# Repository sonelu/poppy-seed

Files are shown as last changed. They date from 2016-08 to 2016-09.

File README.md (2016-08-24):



# Poppy-Seed

This is the little sibling (sister?) of the [Poppy Humanoid](https://github.com/poppy-project/poppy-humanoid) robot developed by the [Poppy Project](https://github.com/poppy-project) team.

At this moment it is in alpha stages and the only thing that can be promissed is that it doesn't catch fire in the first 2 hours of (very limited) operation. Those that are interested to participate in the development of this robot are wellcome, but I cannot stress ehough that things are not in a final form and most of the work involved is not trivial in nature. In time we expect certain items to be provided ready-made instead of needing to hack them from scratch, therefore simplifying the construction.

## Preliminary documentation
Before going into the details of the project there are a few documents that may be useful to read:
* [Torque and design]: a document that explains the main assumption behind the belief that Poppy Seed will work.
* [High level design]: the main design considerations for Poppy Seed.
* [3D Printing guide]: as one of the goals of Poopy Seed is to be printed on a home 3D printed, I included in this document the main tips about printers, materials, finishing and others.

## Poppy Seed
Here are the main links to the project:
* [BOM](hardware/BOM.md). The list of parts needed for the building of a Poppy Seed robot
* [3D Model](https://cad.onshape.com/documents/56e0876fe4b0cd61903da4dc/w/bd94978c48e4f7f7abc728f0/e/cfad6e13d76618b39ab2a28a). This is the link to the OnShape 3D model of the Poppy Seed robot. You can access it freely and in case you want to participate in the development, please send me a share request.
* [3D Parts](hardware/3d parts/). This is the main page for the STLs for the robot.
* [Assembly guide](docs/assembly/README.md). This is the entry page for the robot assembly guide.
* [Electronics](hardware/electronics/). This is the entry page for the electronics used in the project. Please read carefully before starting this project.
* [Setup]. A document providing the steps needed to setup the robot for use.

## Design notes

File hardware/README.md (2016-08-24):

# Hardware

This section contains information about the hardware parts that are needed for the build of your Poppy Seed.

First have a look at the [BOM](BOM.md) file and make sure you understand all the parts that are needed. As this is a very early version of the robot some parts are custom-built. Some things are easy, but there are also parts that require soldering  and tools that you might not have laying around. So please take your time and read through the documents and understand what are the expectations <u>before</u> you place the orders for the materials needed.

If you plan to print the 3D parts youself read the document [3D Printing Guide] and make sure you understand the complexities of this process. If this is your first time in 3D printing I don't think it is a good idea to have Poppy Seed as your first project. A good knowledge of your 3D printer capabilities and limitations will save a lot of effort, time and money. The directory <b>"3D parts"</b> contain all the STLs that are needed. 

Once you have the parts you can start putting the robot together. The [Assembly guide](../docs/assembly) will walk you through this process, including the setup of the electronics.

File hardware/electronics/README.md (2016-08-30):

# Electronics

This section provides details about the custom or customised electronics used in Poppy Seed.

* [Hot-Swap board](hotswap.md): this boards are placed in the shins and they are used to control the power flow from the batteries to the Dynamixel bus allowing us to hot-swap the batteries
* [XL hub](xlhub.md): this is a small board that allows us to connect up to 5 XL cables together and has standard 4mm mounting holes that will give us the ability to position it on the side of a servo
* [Custom HAT with Dynamxiel bus controller, power regultors and 9DOF IMU]: this HAT (board that fits on top a Raspberry Pi) is a temporary solution until Hipi becomes avaialable
* [Audio amplifier]:
* [Raspberry Pi on a diet]: this is a standard Raspberry Pi with the USB and Ethernet connectors removed and replaced with some simple JST 4-pin connectors. This reduces significatly the weight of the board and saves a lot of space for connectivitiy (since the USB connectors are extremely bulky for our need)
* [A custom USB adapter for dongles]
* [A custom USB cable - very short for the Dynamixel bus controller]

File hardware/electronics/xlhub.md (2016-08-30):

# Dynamixel XL hub

Unlike the AX bus, there is no original [Robotis hub](http://www.robotis-shop-en.com/?act=shop_en.goods_view&GS=1398&GC=GD080300) that allows you to connect together several Dynanixel cables for XL bus. It is quite easy to put this together with a little bit of soldering skills.

You will need:
* a small prototyping board - preferrably one with stripes
* 5 [MOLEX microblade board connectors](http://uk.farnell.com/molex/53253-0370/header-2-0mm-3way/dp/1756921)

As tools you will need:
* a soldering iron
* solder
* small pliars
* a drill with a 4mm bit
* a hand saw (to trim the board)

The board as seen on the component face looks like this:

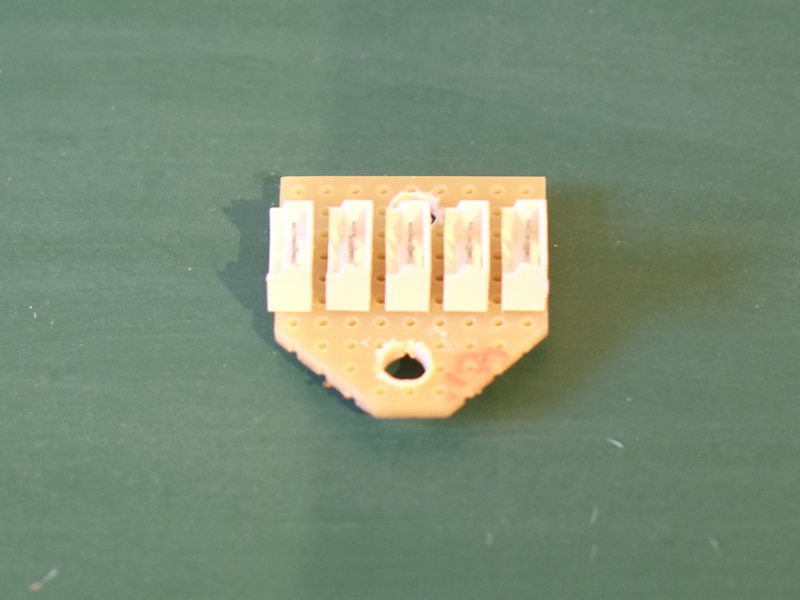
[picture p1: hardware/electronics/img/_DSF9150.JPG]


Cut the board so that you have 9 x 10 holes availalable. We will solder the 5 MOLEX connectors alon those 9 holes while the vertical 10 holes will allow us to drill 2 4mm holes at aproximately 18mm distance.

Solder the 5 MOLEX connectors on the boards and connect them pin to pin. The following picture should give you an idea of the back of the board:

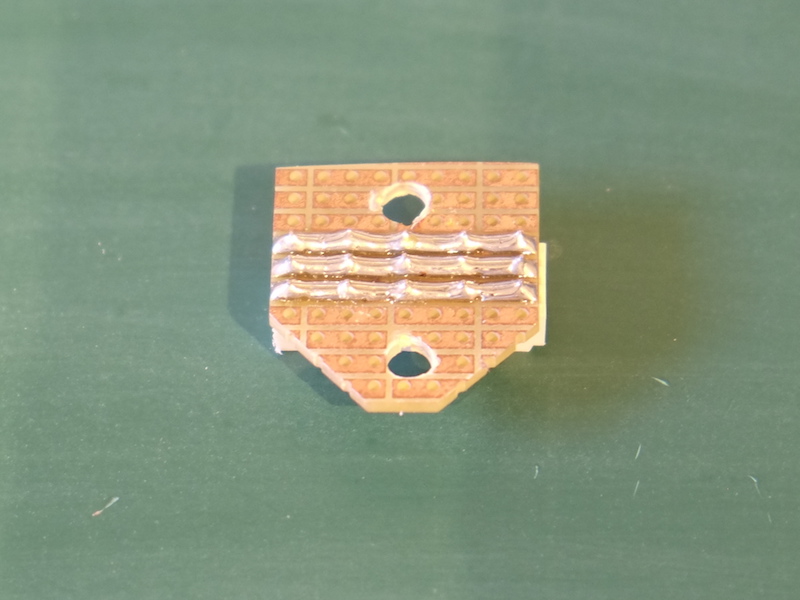
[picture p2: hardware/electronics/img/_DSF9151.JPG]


The board has normally 2.54 pitch and the MOLEX connectors have 2mm. Don't be put off by this: gently push the exterior connector a little so that they can be placed in the holes, then presss firmly the connector onto the board. You will see that you can press it all the way until the bottom of the connector is in contact with the board. Solder the connector on the back. Then, looking at the pins of the connector you will see that they have been bent towards the center of the connector. Take a small pliers and simply straighten them back to the vertical position. Repeat this for all the 5 connectors.

Now make two 4mm holes at 7 holes distance = 17.78mm. This is good enough to allow us to mount this board on the side of a servo using the mounting holes that have 18mm. When making this holes the best is to use 2mm, 3mmm and then 4mm drills instead of going straight to the 4mm drill. You will have less changes for your drill to slip one side or the other.

When you're done cut the corners of the board as you see in the pictures. This will reduce the risk of faulting moving parts from the robot while the board is in position close to joints.

You will have to prepare two of these boards for a Poppy Seed, one for the upper torso and one for the lower torso.

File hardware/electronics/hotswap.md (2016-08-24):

# Hot-Swap board

For Poppy Seed we will use LiPo batteries to power the Dynamixel bus as well as the electronics. We will use two LiPo batteries (2S - 1000mA) each one located in the foot. Using two batteries provides a number of advantages:

* equal distribution of weight
* more capacity (2 x 1000mA)
* ability to swap the batteries one by one thus reducing the need to power down the electornics (mainly the Raspberry Pi)
* because the batteries a positioned in the lowest possible place it reduces the position of the center of mass for the robot, improving stability

In order to be able to use 2 LiPo batteries in parallel and expecially to allow hot-swapping of the batteries (ex. removing one of the batteries that is discharged and replacing it with a fresh battery) we need to control the way the current flows between these batteries. If we connect the batteries blindly in parallel, when batteries are discharged (ex. aprox. 7V or bellow) and one of the batteries is replaced with a new battery (ex. aprox. 8.4V) the difference in potential between the two batteries will produce a so called "rush current" - practically it is as if the new battery is shorted. This is extrmely dangerous as the currents can reach (for short period of time, true) 2-3 times more than the dicharge current that the battery can support.

To avoid this scenario we need to place in series with the battery a diode that allows the current to flow in only one direction (from the battery to the consumer) thus blocking the flow towards the battery (which happens for instance in the case of the discharged battery). A simple diode might foot the bill here provided that it is dimensioned corectly for the power disipassion needed. A typical silicon diode has a forward voltage of 0.7V - meaning we will loose 0.7 V from the battery voltage. In our case this is not very good news because we will loose aprox 10% of the 2S LiPo voltage which is not acceptable. Additionally with an expected current of 2A going through this diode we would have a power dissipation of 0.7V x 2A = 1.4W which will be quite a hefty diode. And a hot one indeed.

The alternative is to use a diode with a forward voltage as lower as possible. This is what the Schottky diodes are for: their forward voltage is in the range 0.35V, some even lower. That means lower power consumption (and heat) as well as less loss of potential from the battery.

The most elegant solution though is to use the Texas Instruments' [SM74611KTTR](http://uk.farnell.com/texas-instruments/sm74611kttr/hot-swap-controller-30v-to-263/dp/2492333) hot swap controller that is designed for the current flow in photovoltaic pannels. This is an actually complex device that includes a high power MOSFET (that ensures a low forward voltage) and a sophisticated charge pump and controller that ensures a very low power consumption and very high efficiency. The forward voltage these "smart bypass diodes" is typically 28mV!

The board for the Poppy Seed hot-swap is build with such a smart diode and it includes in addtion:

* 2 [MOLEX connectors 52253 Micro-Latch](http://uk.farnell.com/molex/53253-0370/header-2-0mm-3way/dp/1756921)
* One 2 pin standard 2.54 pin header
* a small prototyping board

The two Molex connectors and the smart diode is placed on one face of the board:

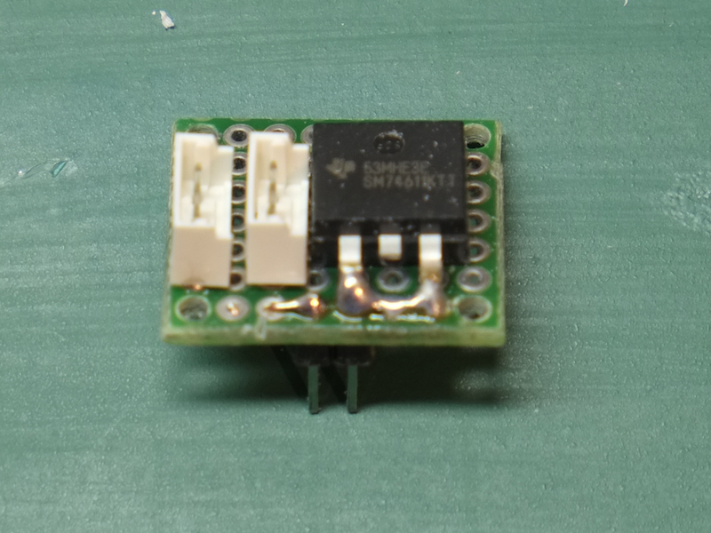
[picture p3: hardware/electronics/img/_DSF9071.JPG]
_DSF9071


While the 2-pin head is on the other side:

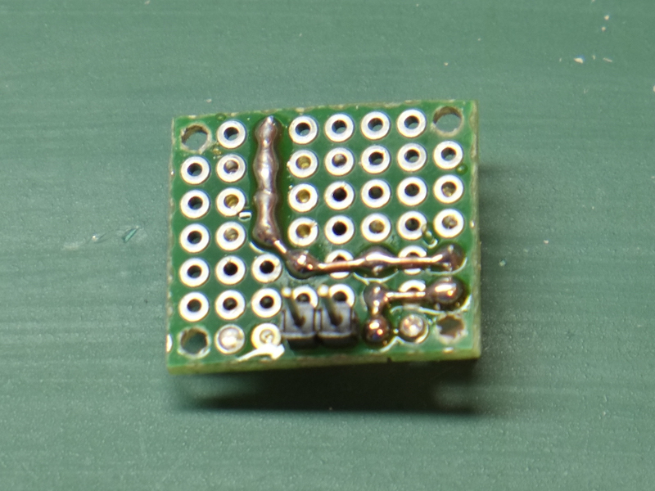
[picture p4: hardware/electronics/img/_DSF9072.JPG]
_DSF9072


The connections are pretty intuitive:

* the pin-head as seen from the side with the parts (the first picture above) is connected with the right pin to the + of the battery and the left pin to the - of the battery. This is controlled by the hole at the back of the shin that allows you to connect the battery in only one way
* the + from the pin is connected to the anode of the diode (the pins)
* the cathode of the diode (the DAP area) then connects to the VCC pins of the Dynamixel bus (center of the two MOLEX connectors)
* the - from the battery connects to the GND pins of the Dynamixel bus (the lower pins in the first picture)
* the 2 MOLEX pins are connected pin-to-pin as you can see in the second picture

The board has 4 holes in the corners with 17.78mm horizontal distance between them (7 standard 0.1' holes) and 15.24mm vertical distance (6 holes). This is the distance between the supports in the shin.

When the battery is connected in the 2 pins on the back side it will inject the voltage into the Dynamixel bus that is connected to the MOLEX connectors. If there is already voltage in the bus (for example there is already another battery on the chain) and that voltage is higher than the voltage of our battery then the diode will break the circuit and our battery will no longer be connected to the bus (this is the case of a discharged battery). If the voltage of our battery is higher than the existing voltage of the chain (if any) than the diode will let the current flow through the circuit, powering the bus.

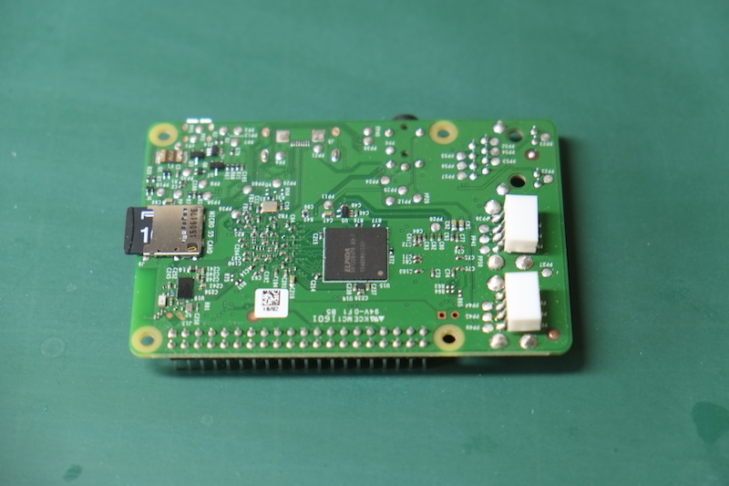
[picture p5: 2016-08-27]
hardware/electronics/img/_DSF9110.JPG

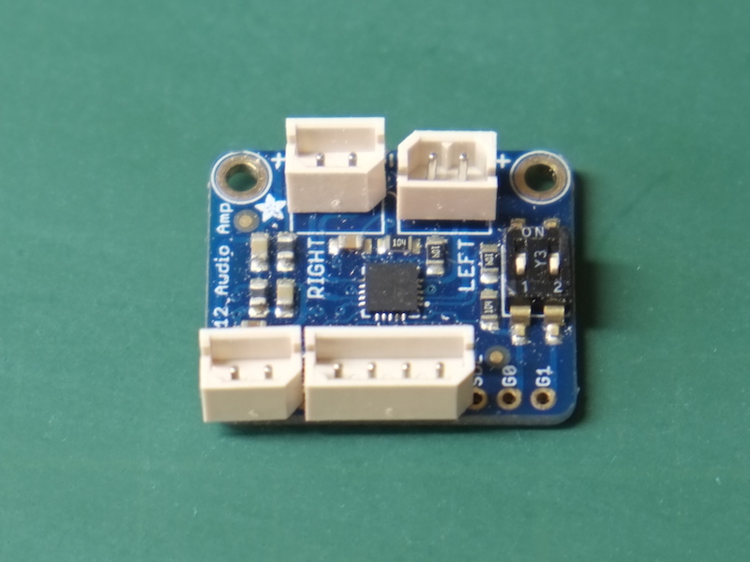
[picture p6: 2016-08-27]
hardware/electronics/img/_DSF9108.JPG

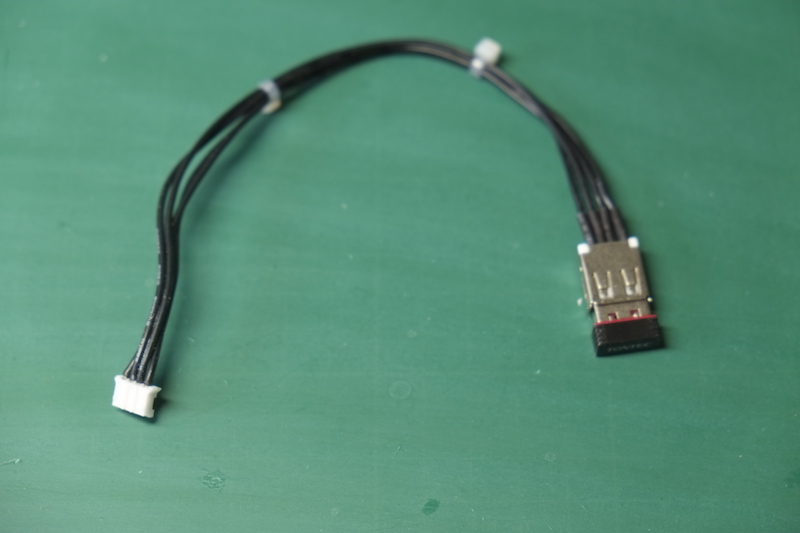
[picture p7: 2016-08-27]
hardware/electronics/img/_DSF9114.JPG

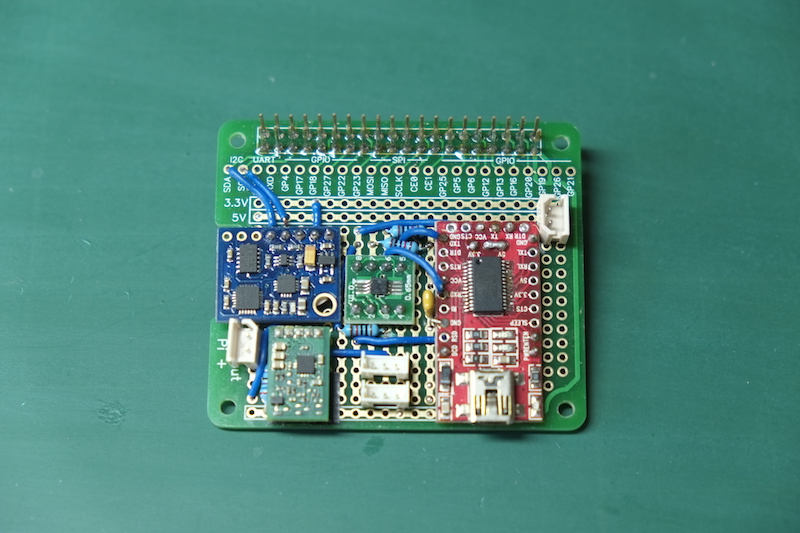
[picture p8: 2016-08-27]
hardware/electronics/img/_DSF9112.JPG

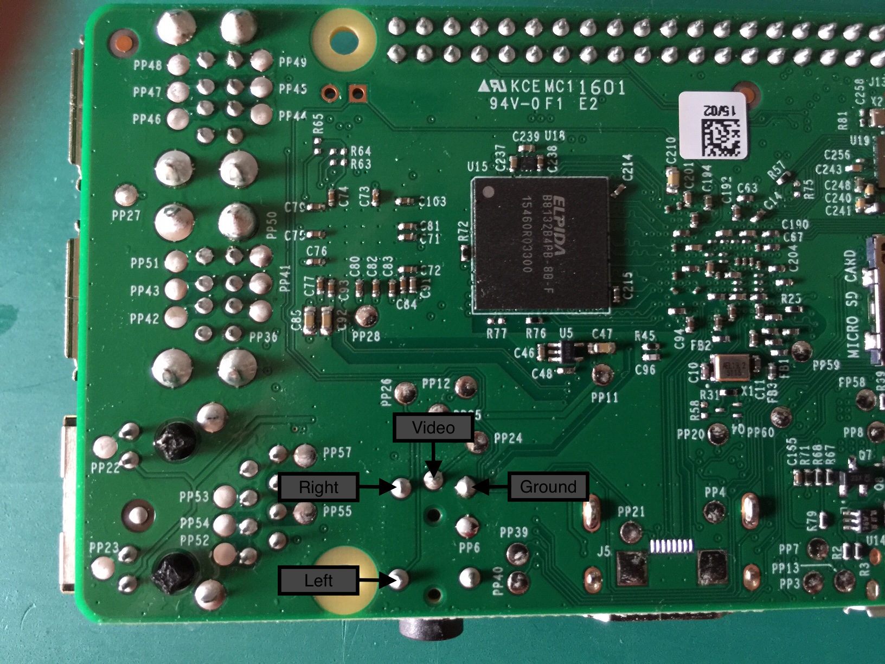
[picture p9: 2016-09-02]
hardware/electronics/img/audio.jpg

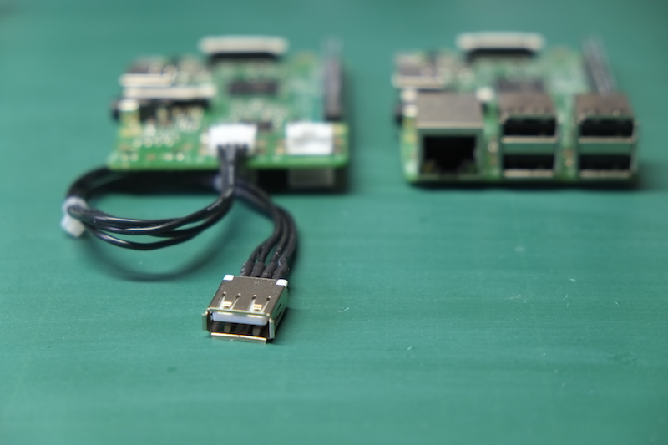
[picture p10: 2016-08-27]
hardware/electronics/img/_DSF9115.JPG

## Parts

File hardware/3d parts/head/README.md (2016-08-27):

# 3D Parts for Head

These are the STL files for the parts that are needed to build the Poppy's head.

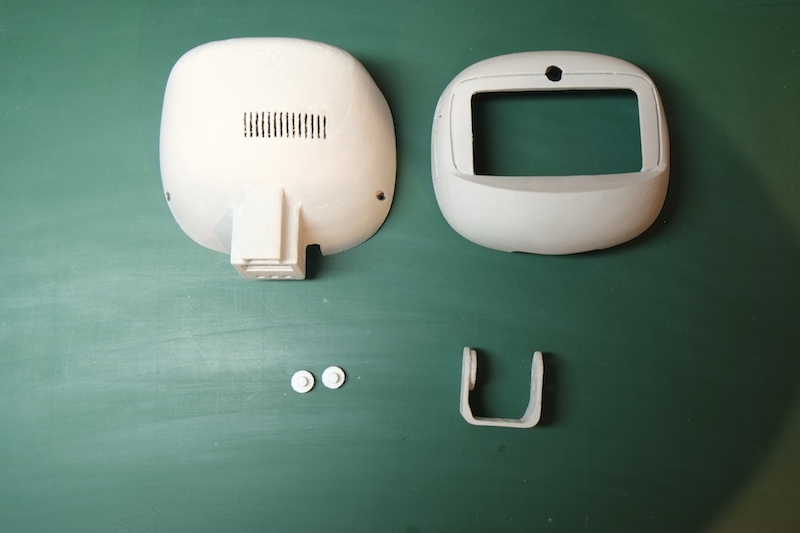
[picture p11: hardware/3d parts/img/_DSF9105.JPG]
Head


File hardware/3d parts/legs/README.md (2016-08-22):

# 3D Parts for Legs

These are the STL files for the parts that are needed to build the Poppy's legs.

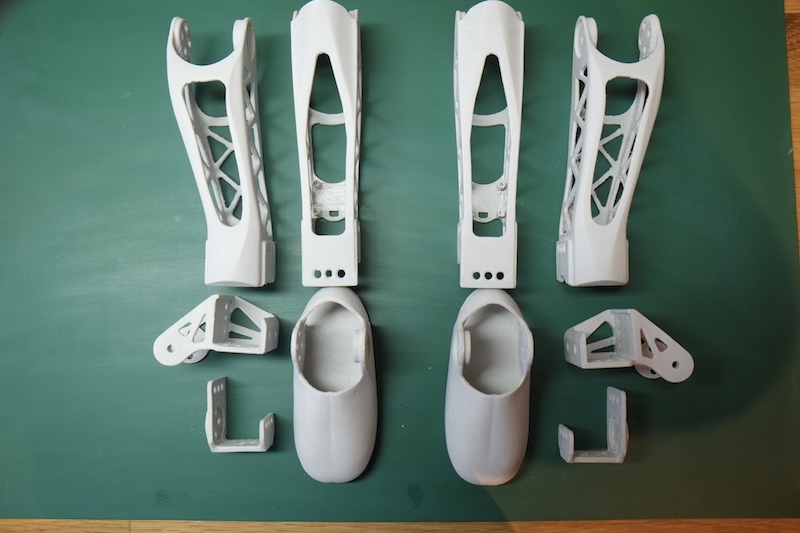
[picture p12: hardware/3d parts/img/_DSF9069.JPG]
Legs


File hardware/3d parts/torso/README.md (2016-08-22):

# 3D Parts for Torso

These are the STL files for the parts that are needed to build the Poppy's torso.

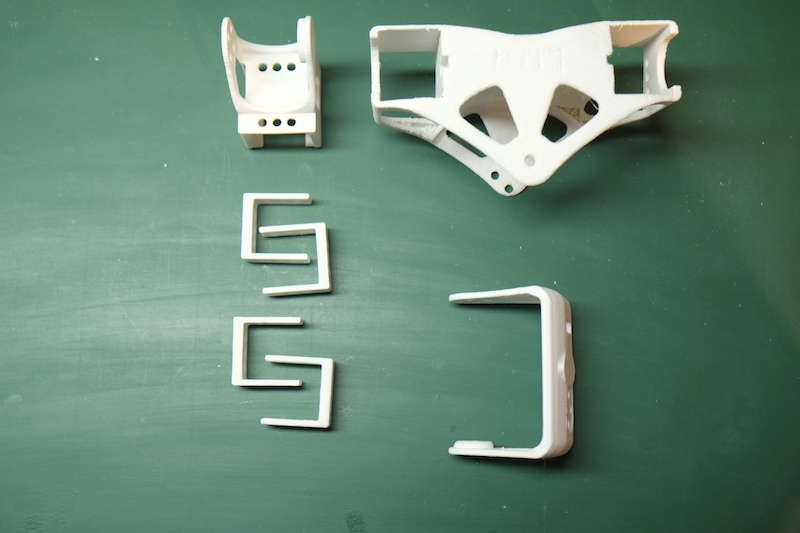
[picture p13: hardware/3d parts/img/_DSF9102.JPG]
Torso


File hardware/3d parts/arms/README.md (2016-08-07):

# 3D Parts for Arms

These are the STL files for the parts that are needed to build the Poppy's arms.

Arms

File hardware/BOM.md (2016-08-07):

# Poppy Seed Bill of Materials

This is the list of materials that are needed for the Poppy Seed:
<table>
<tr>
<th width=25%>Part</th align=center><th>Quantity</th><th>Description</th>
</tr>
<tr><td colspan=4><b>Servomotors</b></td></tr>
<tr><td><a href="http://support.robotis.com/en/product/actuator/dynamixel_x/xl_series/xl-320.htm">Dynamixel XL-320</a></td><td align=center>25</td><td>All the motors for Poppy Seed are XL-320, a very cost effective variant of Dynamixel servomotors that have impressive capabilities in a diminutive body. The servos are widely avaialble at all retailers that specialise in robotics as well as Amazon and eBay. Please refer to the document [Torque and design] to understand more about why they might work in this project.</td></tr>
<tr><td colspan=4><b>3D printed parts</b></td></tr>
<tr><td><i>Arms</i></td></tr>
<tr><td>Hand left</td><td align=center>1</td><td><a href="https://github.com/sonelu/Poppy-Seed/blob/master/hardware/3d%20parts/arms/hand%20left%20small.stl">link to the STL</a></td></tr>
<tr><td>Hand right</td><td align=center>1</td><td><a href="https://github.com/sonelu/Poppy-Seed/blob/master/hardware/3d%20parts/arms/hand%20right%20small.stl">link to the STL</a></td></tr>
<tr><td>Forearm left</td><td align=center>1</td><td><a href="https://github.com/sonelu/Poppy-Seed/blob/master/hardware/3d%20parts/arms/forearm%20left%20small.stl">link to the STL</a></td></tr>
<tr><td>Forearm right</td><td align=center>1</td><td><a href="https://github.com/sonelu/Poppy-Seed/blob/master/hardware/3d%20parts/arms/forearm%20right%20small%20(check).stl">link to the STL</a></td></tr>
<tr><td>Upper arm</td><td align=center>2</td><td><a href="https://github.com/sonelu/Poppy-Seed/blob/master/hardware/3d%20parts/arms/upper%20arm%20small.stl">link to the STL</a></td></tr>
<tr><td>Arm connector</td><td align=center>2</td><td><a href="https://github.com/sonelu/Poppy-Seed/blob/master/hardware/3d%20parts/arms/arm%20connector%20small.stl">link to the STL</a></td></tr>
<tr><td>Shoulder left</td><td align=center>1</td><td><a href="https://github.com/sonelu/Poppy-Seed/blob/master/hardware/3d%20parts/arms/shoulder%20left%20small.stl">link to the STL</a></td></tr>
<tr><td>Shoulder right</td><td align=center>1</td><td><a href="https://github.com/sonelu/Poppy-Seed/blob/master/hardware/3d%20parts/arms/shoulder%20right%20small.stl">link to the STL</a></td></tr>
<tr><td><i>Body</i></td></tr>
<tr><td>Chest</td><td align=center>1</td><td>[link to the STL]</td></tr>
<tr><td>Spine</td><td align=center>1</td><td>[link to the STL]</td></tr>
<tr><td>Abdomen</td><td align=center>1</td><td>[link to the STL]</td></tr>
<tr><td>Dual XL mount</td><td align=center>4</td><td>[link to the STL]. Used to connect two XL servo is a 90 degrees angle.</td></tr>
<tr><td>XL idle</td><td align=center>2</td><td>[link to the STL]. Used to provide the idle support for a dual XL-320 combination.</td></tr>
<tr><td><i>Legs</i></td></tr>
<tr><td>Foot left</td><td align=center>1</td><td>[link to the STL]</td></tr>
<tr><td>Foot right</td><td align=center>1</td><td>[link to the STL]</td></tr>
<tr><td>Shin left</td><td align=center>1</td><td>[link to the STL]</td></tr>
<tr><td>Shin right</td><td align=center>1</td><td>[link to the STL]</td></tr>
<tr><td>Thigh left</td><td align=center>1</td><td>[link to the STL]</td></tr>
<tr><td>Thigh right</td><td align=center>1</td><td>[link to the STL]</td></tr>
<tr><td>Hip connector</td><td align=center>2</td><td>[link to the STL]</td></tr>
<tr><td>Hip left</td><td align=center>1</td><td>[link to the STL]</td></tr>
<tr><td>Hip right</td><td align=center>1</td><td>[link to the STL]</td></tr>
<tr><td>Pelvis</td><td align=center>1</td><td>[link to the STL]</td></tr>
<tr><td><i>Head</i></td></tr>
<tr><td>Head face</td><td align=center>1</td><td>[link to the STL]</td></tr>
<tr><td>Head back</td><td align=center>1</td><td>[link to the STL]</td></tr>
<tr><td>Spacer</td><td align=center>2</td><td>[link to the STL]</td></tr>
<tr><td>Neck</td><td align=center>1</td><td>[link to the STL]</td></tr>
<tr><td colspan=4><b>Electronics</b></td></tr>
<tr><td><a href="https://www.raspberrypi.org/learning/hardware-guide/components/raspberry-pi/">Raspberry Pi 3.0</a></td><td align=center>1</td><td>This is the main controller for the robot. We're using the 3.0 for the WiFi</td></tr>
<tr><td>USB WiFi Dongle</td><td align=center>1</td><td>We will use the built-in WiFi for creating a hotspot this WiFi dongle to connect to an exisiting WiFi network. See more details in the [Setup] document. Any WiFi dongle that has been tested and confirmed working with Rasberry Pi should be fine. The one that I used in my setup is <a href="https://www.amazon.co.uk/Tontec-150Mbps-Adapter-Raspberry-Windows/dp/B010AKMF3Y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">this one</a>.</td></tr>
<tr><td><a href="http://www.waveshare.com/product/modules/oleds-lcds/raspberry-pi-lcd/3.5inch-rpi-lcd-a.htm">Waveshare 3.5inch LCD for Raspberry Pi</a></td><td align=center>1</td><td>I have included this display as it is widely avaialble (search on eBay) and seems to be decently well supported. One of the isues we might have with it is that it uses both CE0 and CE1 SPI channels and that will conflict later with the HIPI board.</td></tr>
<tr><td>Interface HAT</td><td align=center>1</td><td>In principle this should be a HIPI HAT, but until that is avaialble I have hacked together a board that includes the Dynamixel interface, 9DOF IMU and a 3A regulator. Details are in the [Interface HAT] document</td></tr>
<tr><td><a href="https://www.adafruit.com/products/1552">Stereo Amplifier 2X2.1W</a></td><td align=center>1</td><td>Again, this should be provided by the amplifier in the HIPI board. In the meantime we use a common amplifier from Adafruit and we will mount it separately in the head. The module is widely avaialble on eBay and Amazon.</td></tr>
<tr><td>Speakers 20x40mm 2W</td><td align=center>2</td><td>Some common version of speakers. Any 20x40mm format will do as long as they also are rated 2W or more. The particular ones that I used in my robot are the ones sold by <a href="http://www.maplin.co.uk/p/2w-mylar-and-paper-rectangle-speaker-20x40mm-n99fu">Maplin in UK</a>.</td></tr>
<tr><td><a href="https://www.amazon.co.uk/Raspberry-Pi-1080p-Camera-Module/dp/B01ER2SKFS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">Raspberry Pi camera</a></td><td align=center>1</td><td>For image processing</td></tr>
<tr><td>Hot-swap custom board</td><td align=center>2</td><td>This is a custom board made with a very low forward voltage equivalent Schotcky chip that alows us to connect 2 LiPo batteries in parallel without having rush current and to hot-swap one battery at a time when changing them. See the [Hotswap board] for details.</td></tr>
<tr><td>XL connectors hub custom board</td><td align=center>1</td><td>For AX connectors Robotis produces a standard hub board that allows you to hook up multiple cables together. Unfortunatelly there is no equivalent board for the XL cables so I had to build one. In addition this board had 4mm fixing holes that allow it to be placed in position using normal XL rivets.</td></tr>
</table>

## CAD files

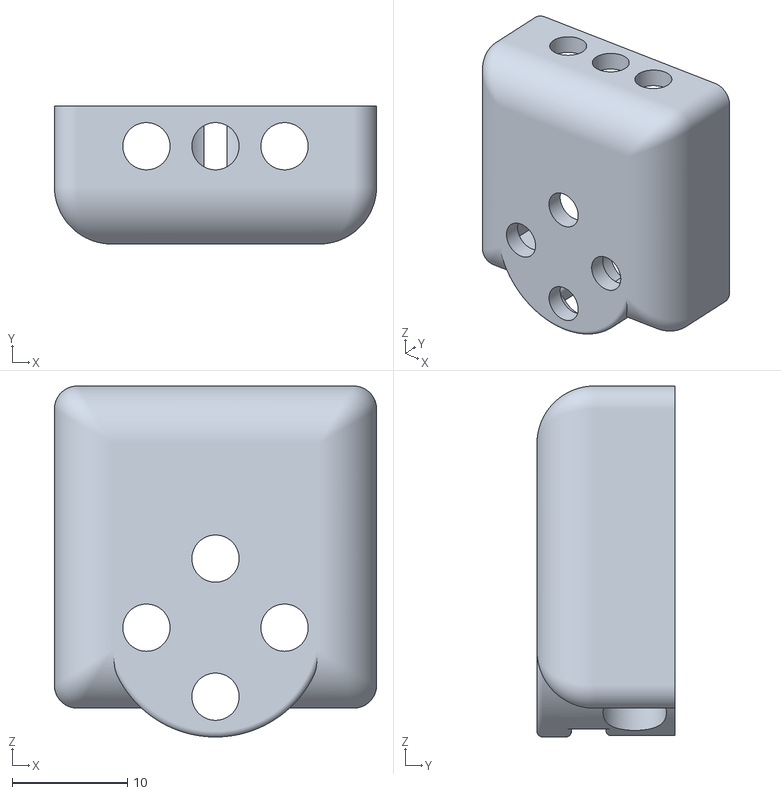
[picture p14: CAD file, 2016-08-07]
hardware/3d parts/arms/arm connector small.stl
28.0 x 12.0 x 30.5

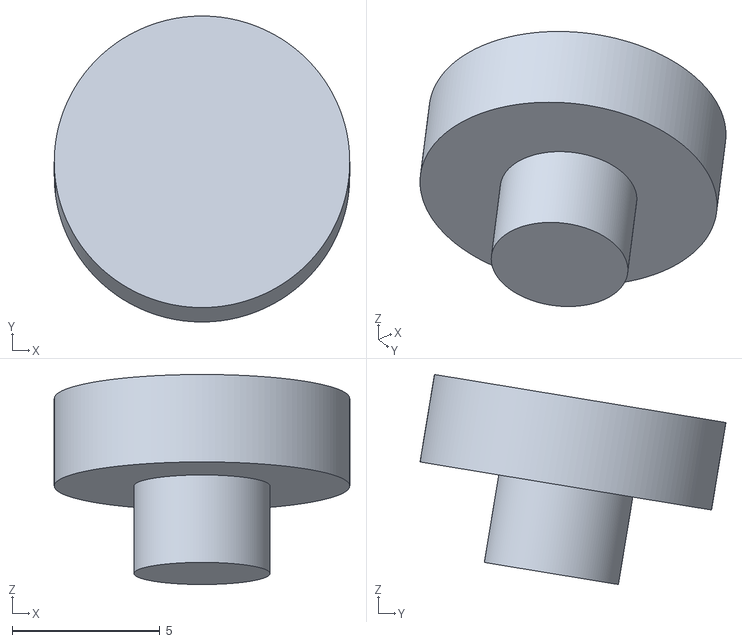
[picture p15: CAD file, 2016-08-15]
hardware/3d parts/head/spacer.stl
10.0 x 10.4 x 7.11

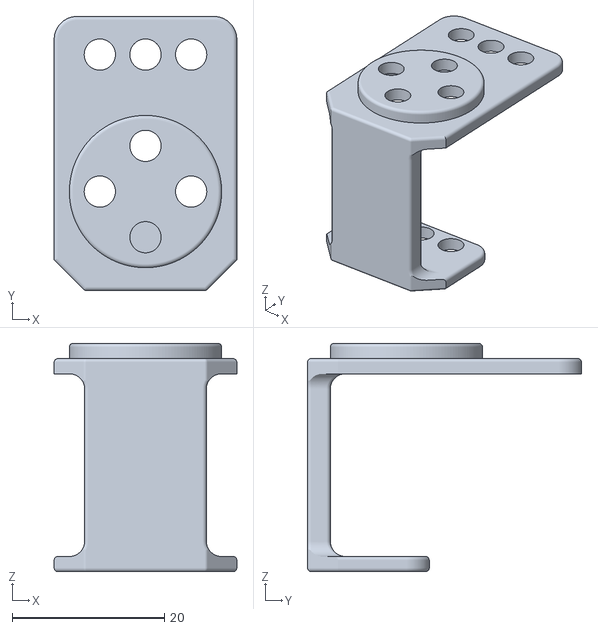
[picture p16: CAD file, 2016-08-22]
hardware/3d parts/legs/hip connector.stl
24.0 x 36.0 x 30.0

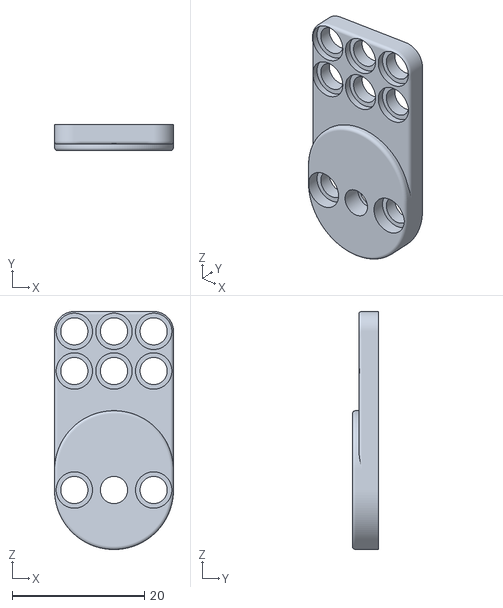
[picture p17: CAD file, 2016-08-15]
hardware/3d parts/torso/dual XL idle.stl
18.0 x 4.00 x 36.0

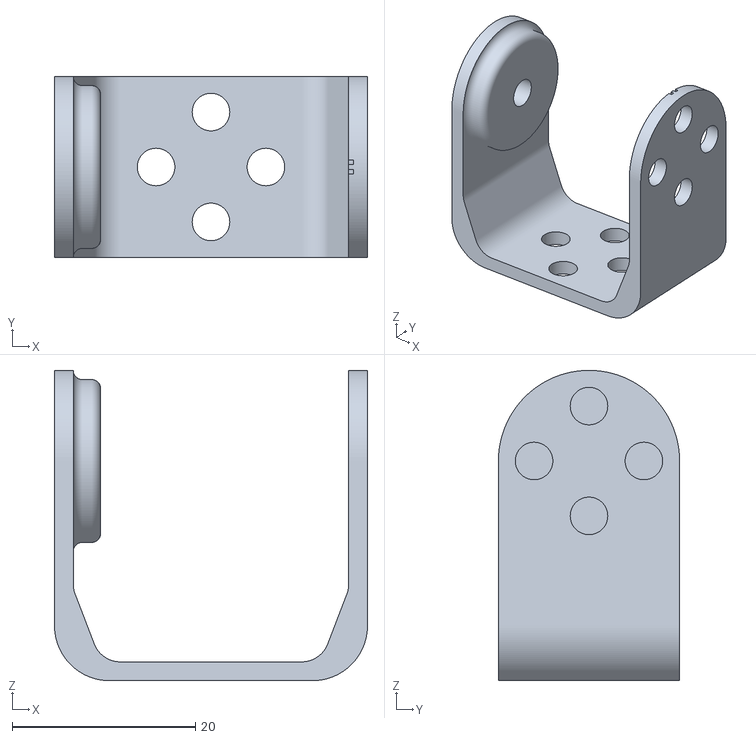
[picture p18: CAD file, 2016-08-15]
hardware/3d parts/head/neck small.stl
34.2 x 19.8 x 33.9

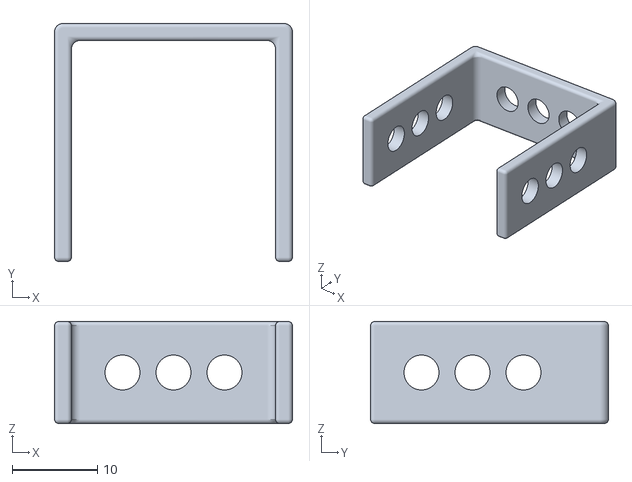
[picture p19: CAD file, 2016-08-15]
hardware/3d parts/torso/dual XL mount.stl
28.0 x 28.0 x 12.0

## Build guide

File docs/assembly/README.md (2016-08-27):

# Poppy Seed Assembly Guide

This assembly guide will provide the main information about how to put together the Poppy Seed robot.

A few preliminary instructions are applicable to all parts assembly:

1. Setting the Dynamixel IDs
2. Setting the servos in 0 position
3. Using the OLLO rivets

The assembly guides are structured by part:

1. [Upper arms assembly](arms.md)
2. [Legs assembly](legs.md)
3. [Torso assembly](torso.md)
4. [Head assembly](head.md)
5. [Putting all together](final.md)

Please note that some of the parts need electronics components ready. They will be mentioned in the detail assebbly instructions for that part.

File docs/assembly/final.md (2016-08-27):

# Final Assembly

You will need:

* the left arm assembled
* the right arm assembled
* the torso assembled
* the left leg assembled
* the right leg assembled
* the head assembled
* the left shoulder 3D printed part
* the right shoulder 3D printed part
* the pelvis 3D printed part
* 2 Dynamixel XL-320 with IDs 11 and 21
* 44 2-step OLLO rivets
* 5 3-step OLLO rivets

We will start by connecting the arms to the torso. First place the left shoulder part onto the servo 41 that is in the torso and secure it with 4 rivets:

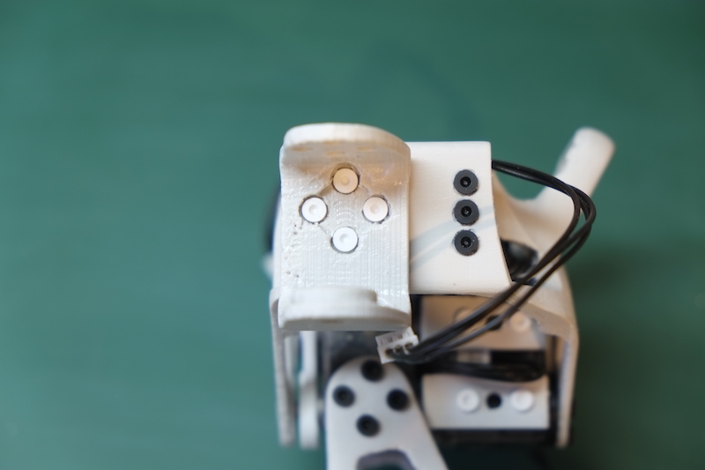
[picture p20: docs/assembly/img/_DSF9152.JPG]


Straighten the shoulder in neutral position and then position the left arm into the shoulder as seen in the picture bellow. Secure it with 4 rivets on the horn side:

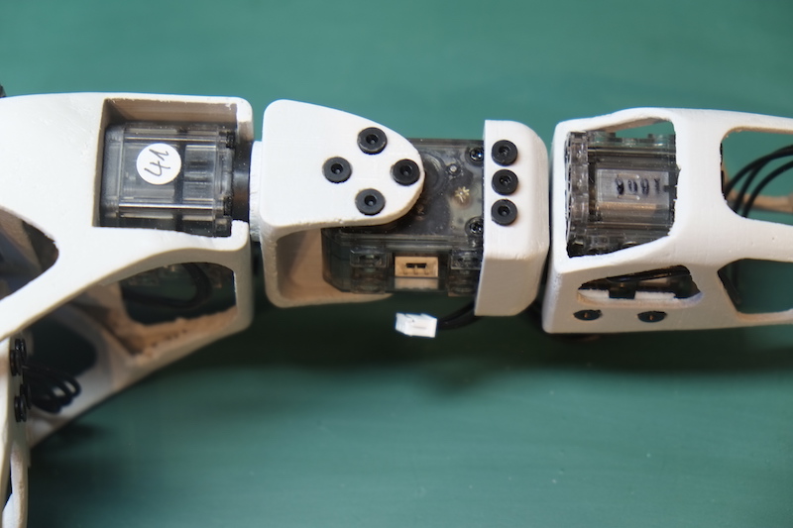
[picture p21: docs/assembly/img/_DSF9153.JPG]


And one 3-step rivet on the idle side:

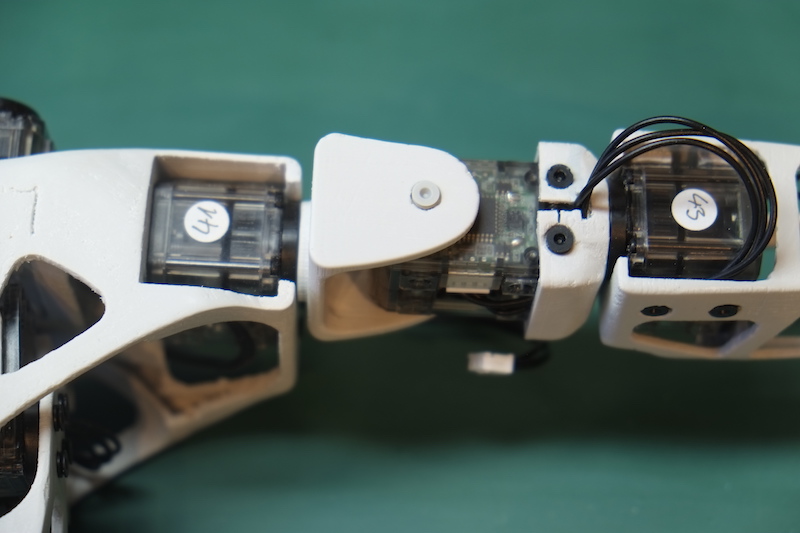
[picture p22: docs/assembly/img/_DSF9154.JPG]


Connect the cable left from the shoulder_y in the torso to the spare connector on the interior of the arm as seen in the picture:

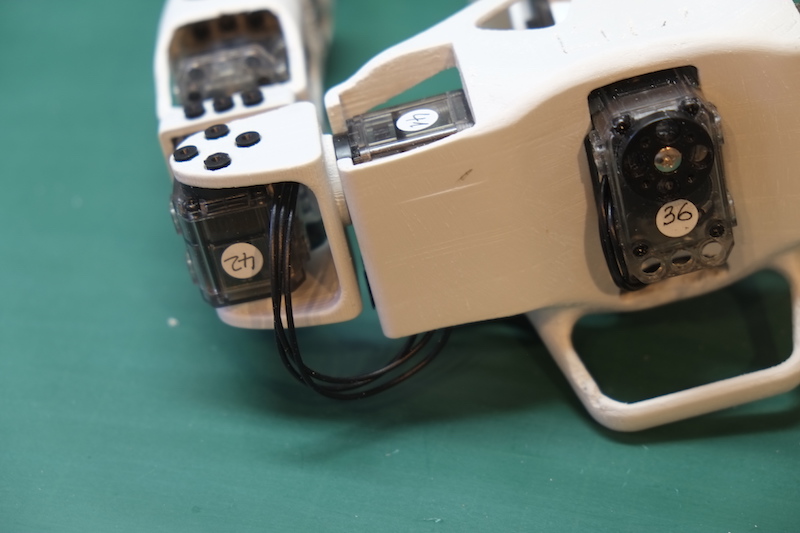
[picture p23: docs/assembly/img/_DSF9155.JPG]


Move around the arm and make sure that the cable does not come in the way of the other parts of the arm.

We will repeat the process for the right side. First secure the right shoulder part using 4 rivets:

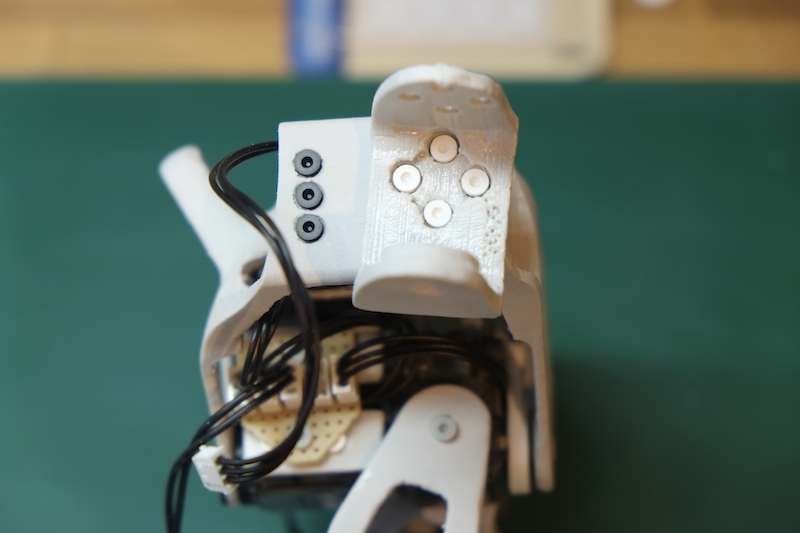
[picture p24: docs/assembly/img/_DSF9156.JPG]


The bring it in neutral position and connect the right arm using 4 rivets on the horn side:

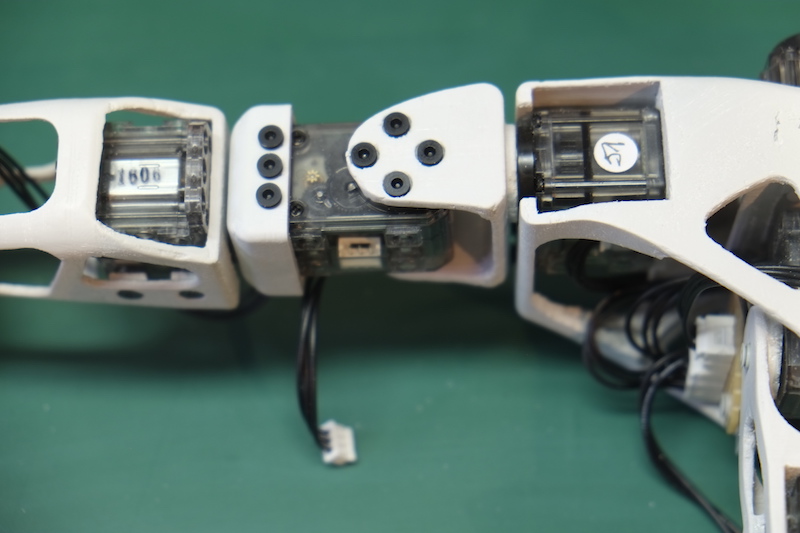
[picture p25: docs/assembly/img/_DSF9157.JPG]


And one 3-step rivet on the idle side:

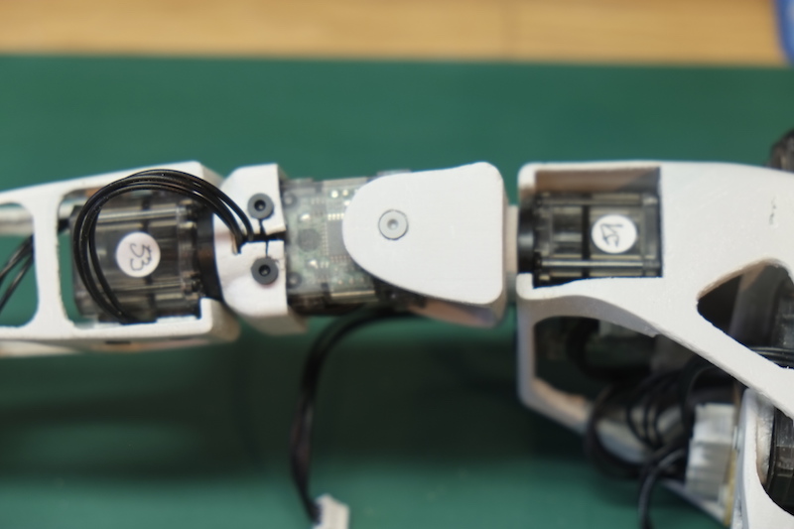
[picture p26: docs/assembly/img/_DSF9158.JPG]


Connect the cable from the servo in the torso to the inside of the arm servo as before:

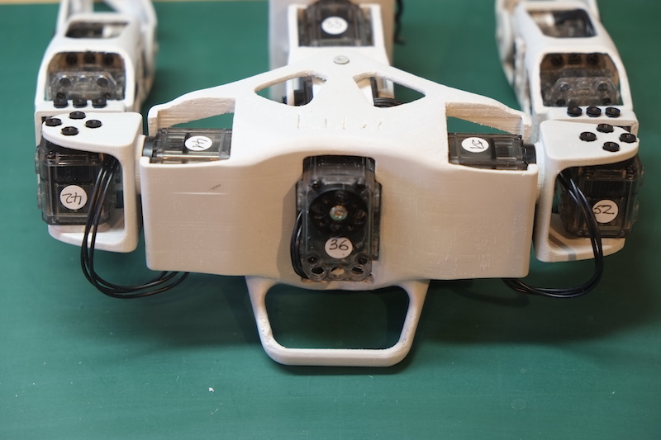
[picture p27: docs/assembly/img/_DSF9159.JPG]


Place the assembled head on the top servo (ID 36) of the torso and secure it in place with 4 rivets:

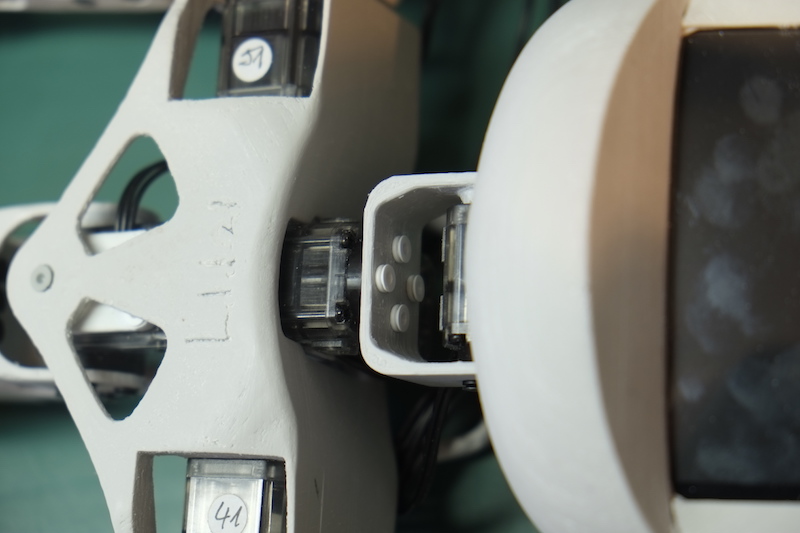
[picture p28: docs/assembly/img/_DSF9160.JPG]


Connect the shorter XL cable from the head_y servo (37) to the remaining connector in the head z (36):

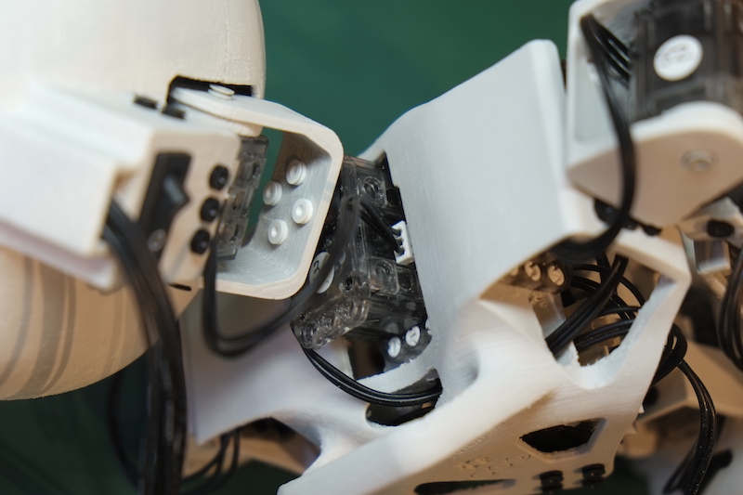
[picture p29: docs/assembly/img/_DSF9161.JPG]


Guide the 300mm XL cable (the shorter one of the two) through the space on one side of the head_z servo (36) so that it arives in the upper part of the torso:

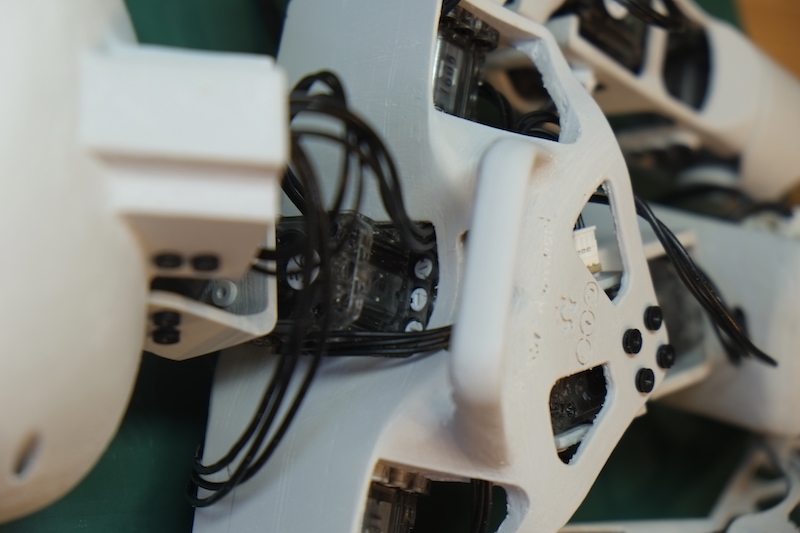
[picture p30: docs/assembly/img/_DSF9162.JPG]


And connect it in the remaining slot in the upper hub in the torso:

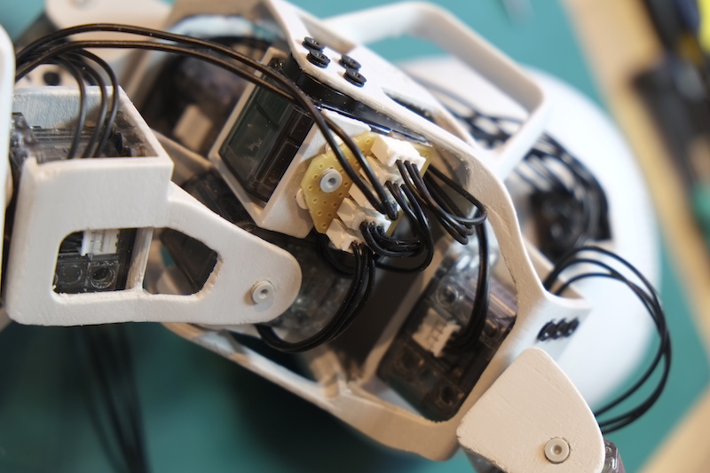
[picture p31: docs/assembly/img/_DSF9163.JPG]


Guide the longer 400mm XL cable through the space on the other side of the head_z servo:

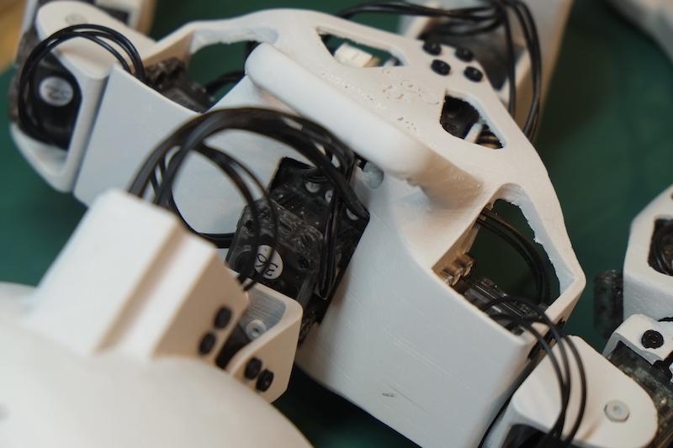
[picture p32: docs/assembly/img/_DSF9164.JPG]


And through the hole in the abdomen:

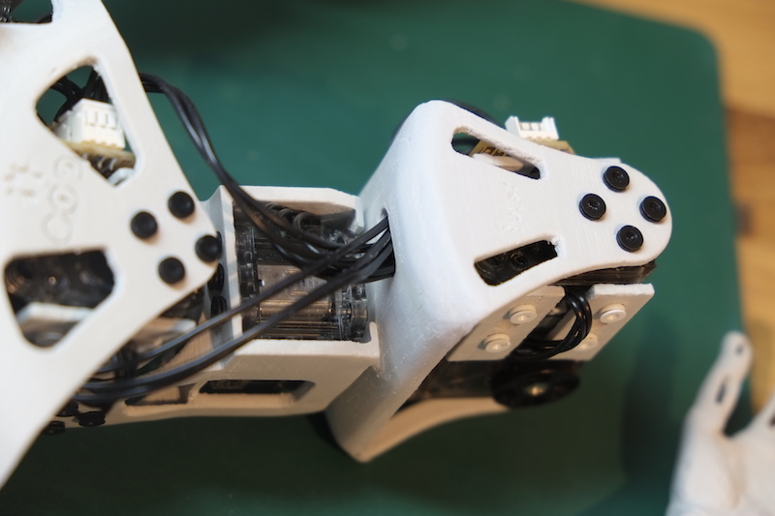
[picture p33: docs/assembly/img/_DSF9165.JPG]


And connect the cable to the empty slot on one side - leaving two slots one next to the other on the other side. These will be used for the buses to the legs:

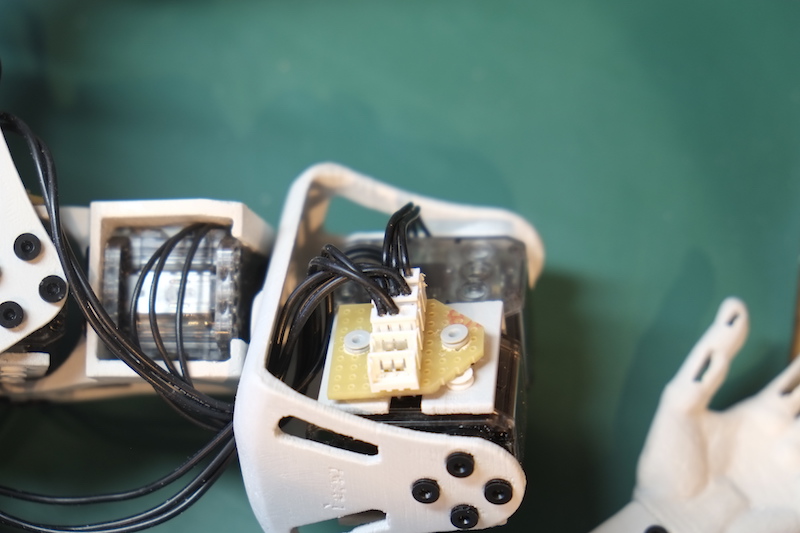
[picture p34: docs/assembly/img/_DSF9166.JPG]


We will start now to assamble the legs. Take the XL-320 with ID 11 and place a normal cable as in the following picture:

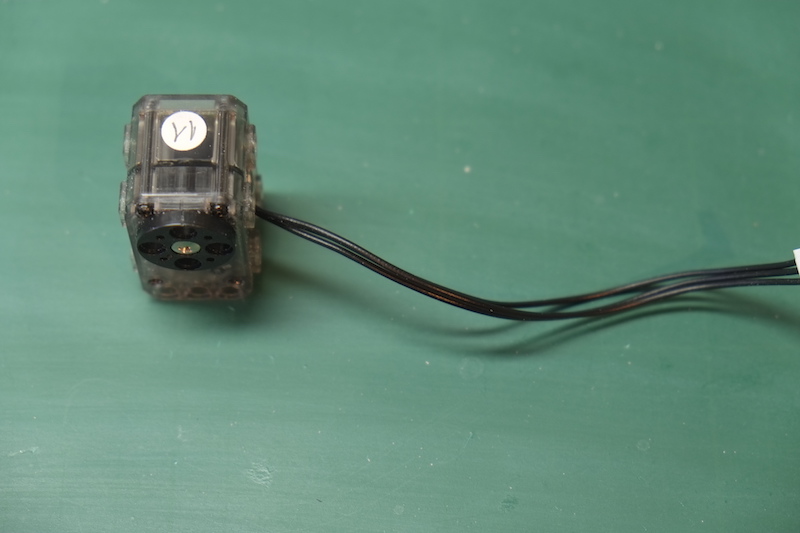
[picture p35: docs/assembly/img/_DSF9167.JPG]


Slide the servo in the pelvis as seen in the picture and secure it with 3 rivets. The cable should be on the outside part:

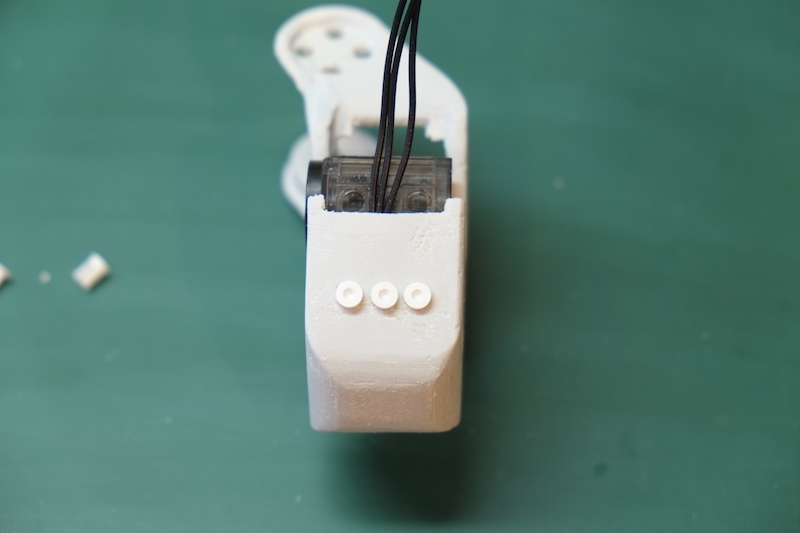
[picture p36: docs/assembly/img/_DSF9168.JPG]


Add 3 more rivets on the back of the pelvis:

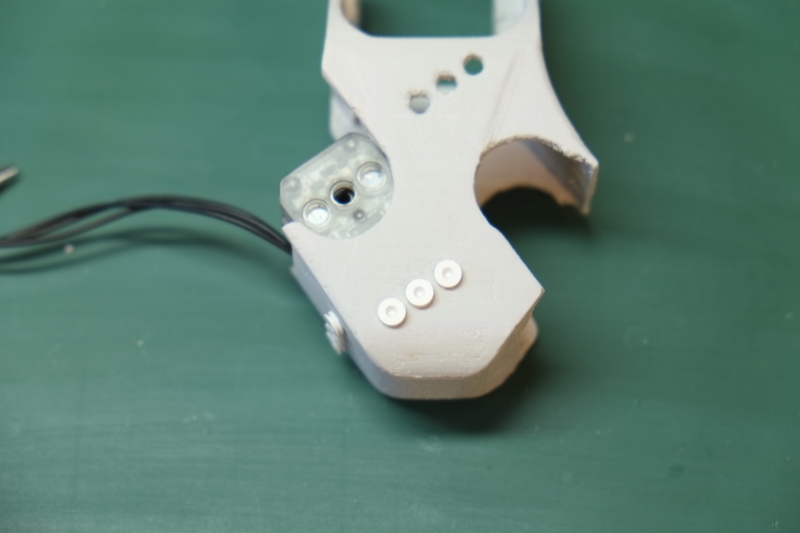
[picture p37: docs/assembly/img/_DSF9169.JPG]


Make sure that the servo is in 0 position. Take the left leg and position it as tight as possible against the pelvis so that you can fix it with 4 rivets as seen in the picture:

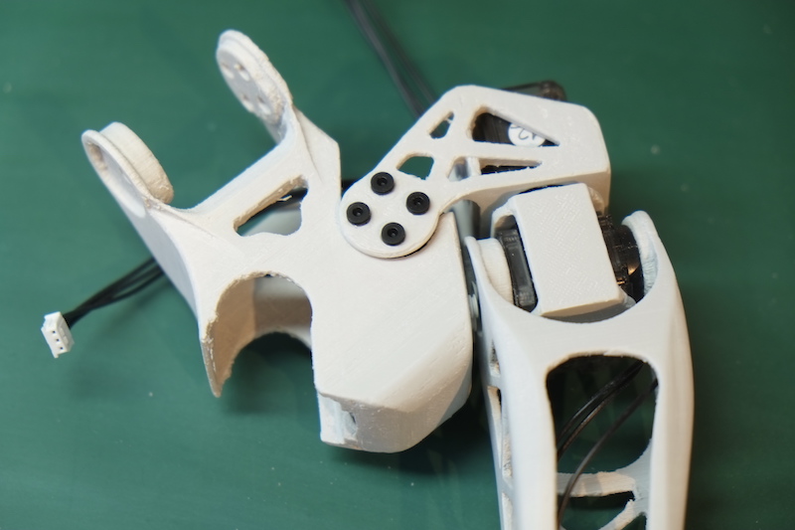
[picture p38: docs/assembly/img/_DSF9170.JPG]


And one 3-step rivet on the idle side:

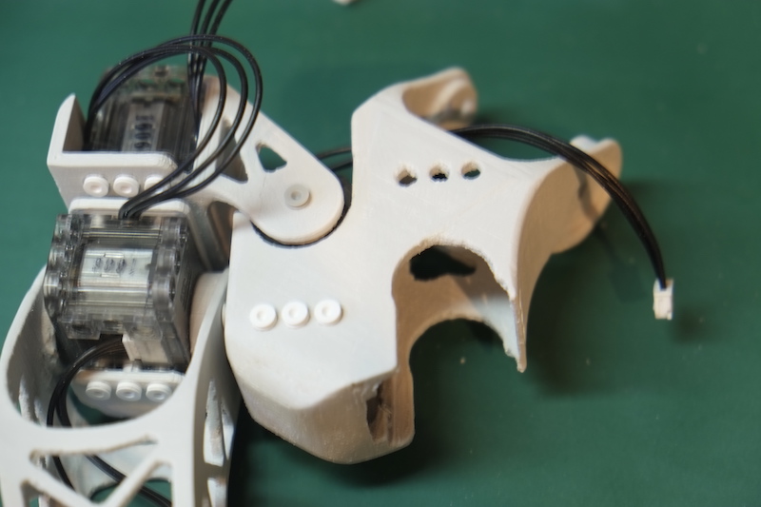
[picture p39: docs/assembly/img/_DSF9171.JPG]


Connect the cable from the leg to the remaining connector in the servo in the pelvis as shown in the picture:

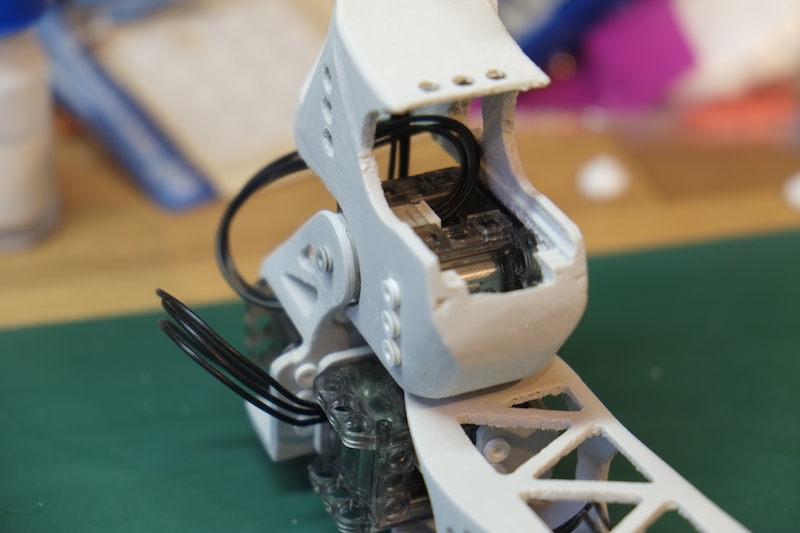
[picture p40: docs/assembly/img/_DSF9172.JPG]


Move the leg around and make sure that the cables do not come in the way.

Take the servo 21 and connect a standard cable as seen in the picture:

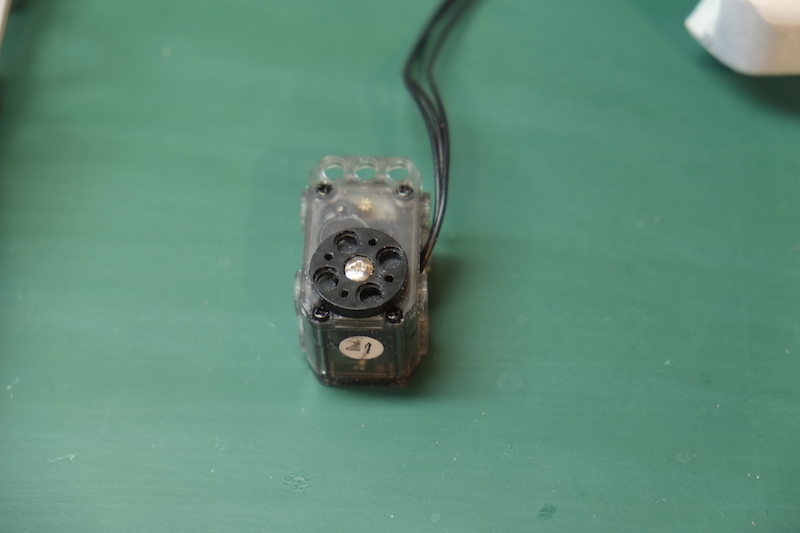
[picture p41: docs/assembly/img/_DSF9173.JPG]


Take the right leg and connect the cable coming from this leg to the remaining connector in the servo 21 making sure that the cable is going through the pelvis as shown in the following picture:

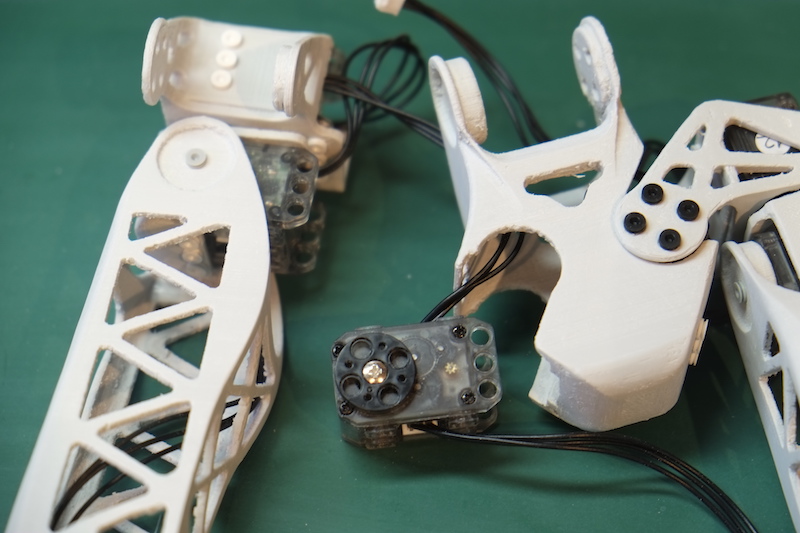
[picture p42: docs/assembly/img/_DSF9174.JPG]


Guide both cables up and slide the servo into the pelvis, then secure it with 3 rivets on the side:

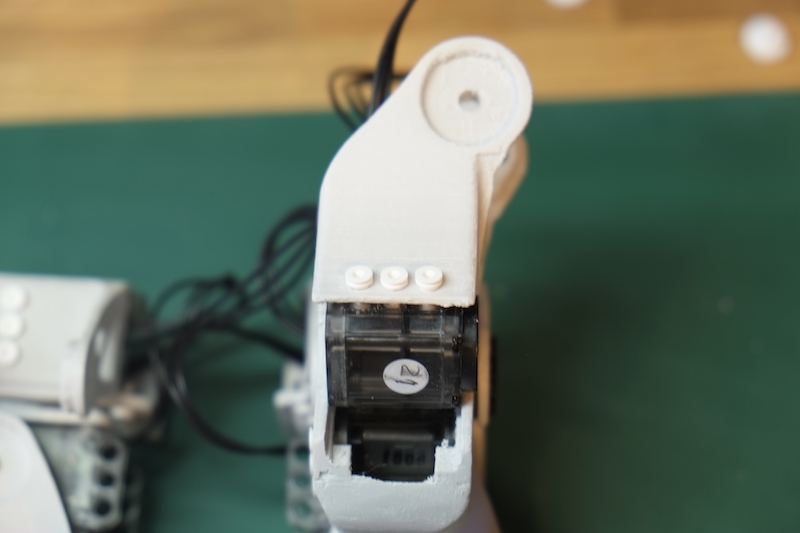
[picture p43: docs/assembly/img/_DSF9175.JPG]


Add 3 more rivets on the back:

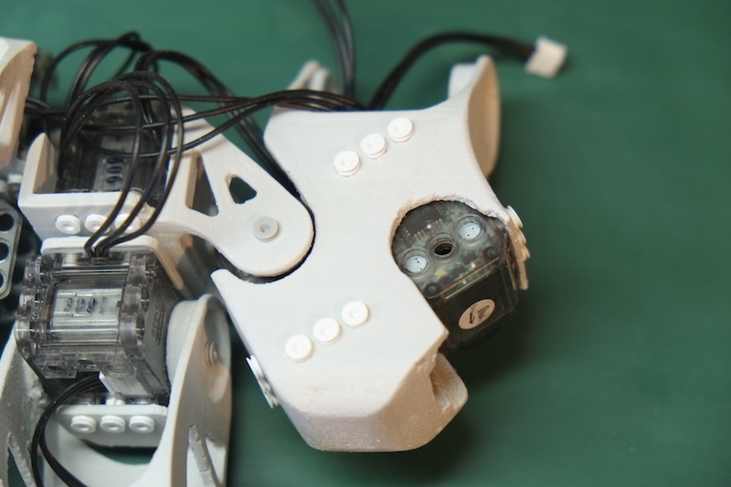
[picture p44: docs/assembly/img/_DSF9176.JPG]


Make sure the servo 21 should be in 0 position. Position the right leg on the servo so that you can secure it with 4 rivets. It will be pointing towards left as you look directly at the assembly:

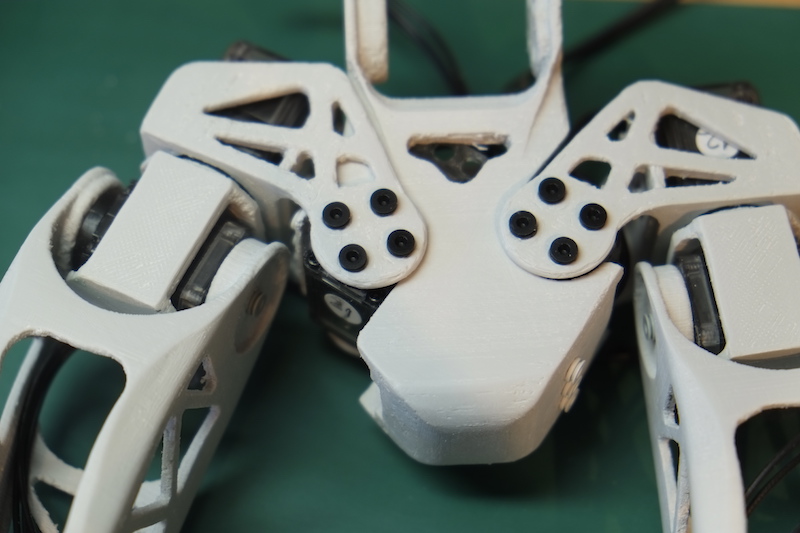
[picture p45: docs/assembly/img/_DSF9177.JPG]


And one more 3-step rivet on the idle side:

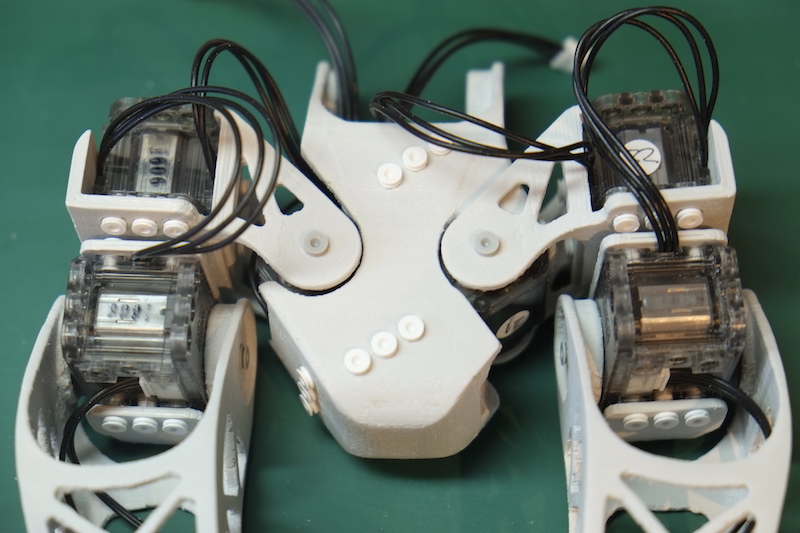
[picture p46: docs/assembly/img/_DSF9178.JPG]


Place the lower torso into the pelvis supports and secure it with 4 rivets:

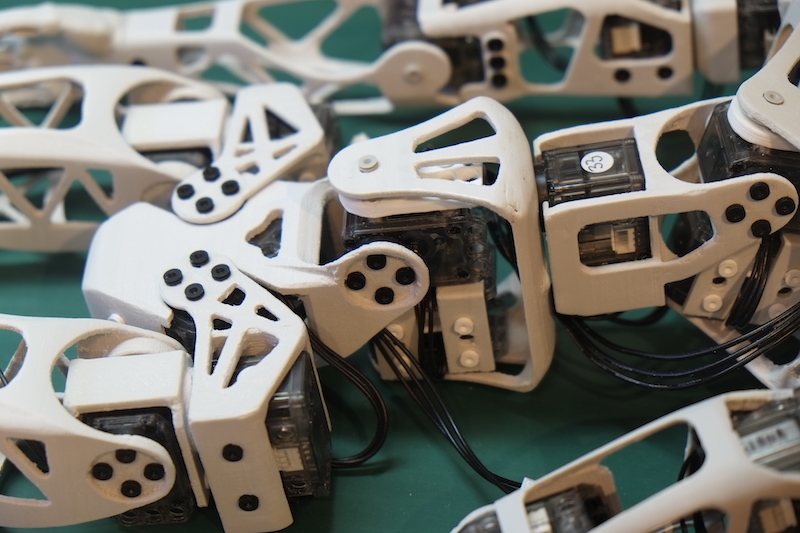
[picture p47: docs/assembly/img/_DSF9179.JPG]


Plus one more 3-step rivet on the idle side (that's the last rivet!)

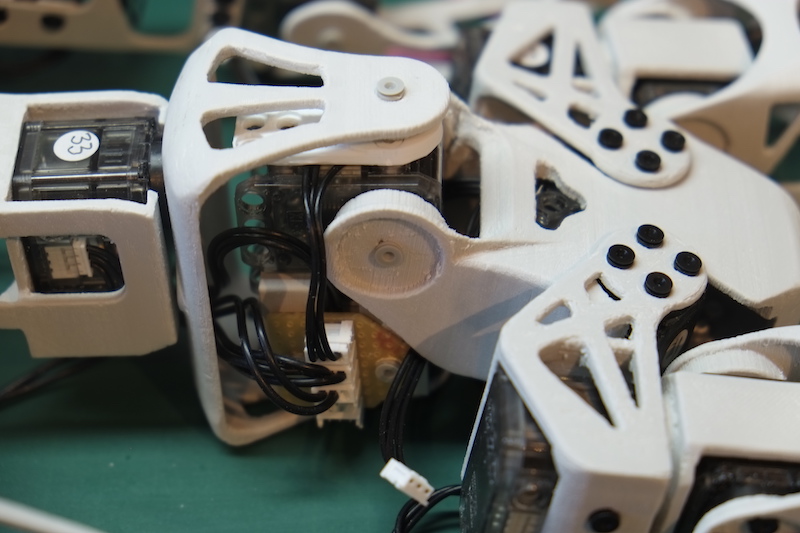
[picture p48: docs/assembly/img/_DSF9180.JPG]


Connect the two cables from the legs to the hub in the lower torso:

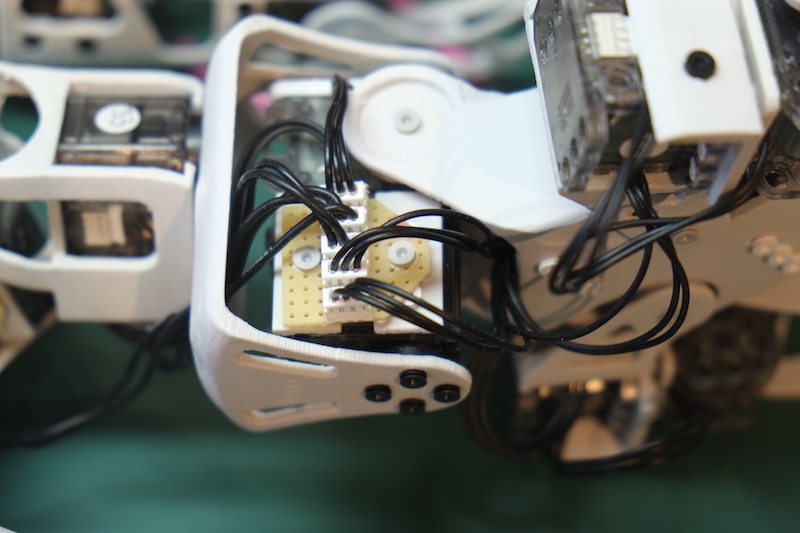
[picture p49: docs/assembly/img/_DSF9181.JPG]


And we're done! Poppy Seed is now complete:

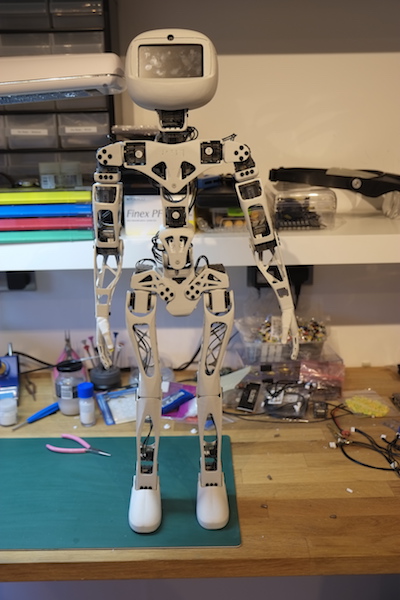
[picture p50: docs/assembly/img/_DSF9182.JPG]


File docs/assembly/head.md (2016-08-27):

# Head Assembly

For the assembly of the head you will need the following parts and fixings:

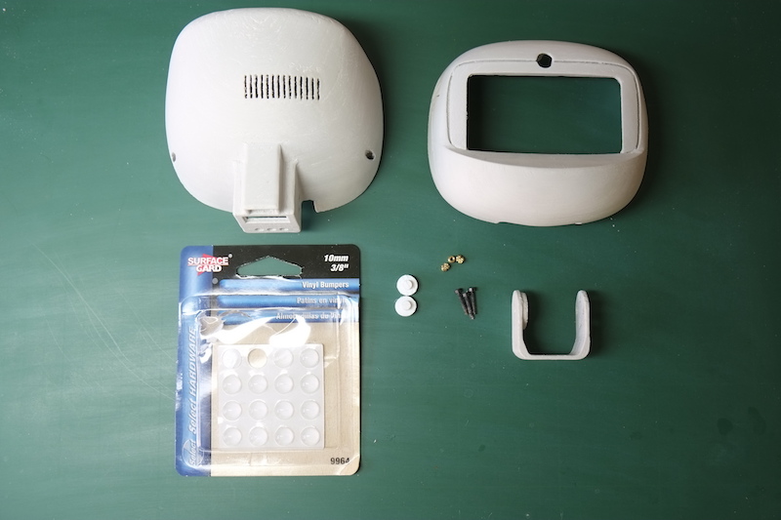
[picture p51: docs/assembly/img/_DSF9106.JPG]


* Head front 3D printed part
* Head back 3D printed part
* Neck 3D printed part
* 2 x spacers 3D printed parts - these are used to support the eletronics inside the head without needing screws; they are made so that you can adjust and print them using the particular settings of your electronics, without needing to reprint the whole back head
* 2 surface guards 10mm bumbers
* 3 2mm heat inserts (I've been using these for a while and I quite like this approach; the ones I use are produced by TR Fastenings in UK, but there are many sellers on eBay - just search for "heat sert". If the community finds it hard to use these heat serts we can produce a variant of the front head that might use normal hex nuts).
* 3 M2x12mm screws (I'm using Allen screws but any would do)
* 4 [M2x12mm F-F standoffs](http://www.ebay.co.uk/sch/i.html?_from=R40&_trksid=m570.l1313&_nkw=f-f+m2+standoff&_sacat=0) 
* 2 M2x15mm M-F standoffs
* 6 M2x6mm screws
* 11 2-step OLLO rivets
* 1 3-step OLLO rivet
* One XL-320 servo with ID 37
* One standard XL Dynanmixel cable

You would also need to have the following electornics prepared (follow the guides in the [Electronics](https://github.com/sonelu/poppy-seed/tree/master/hardware/electronics) section about preparing them):

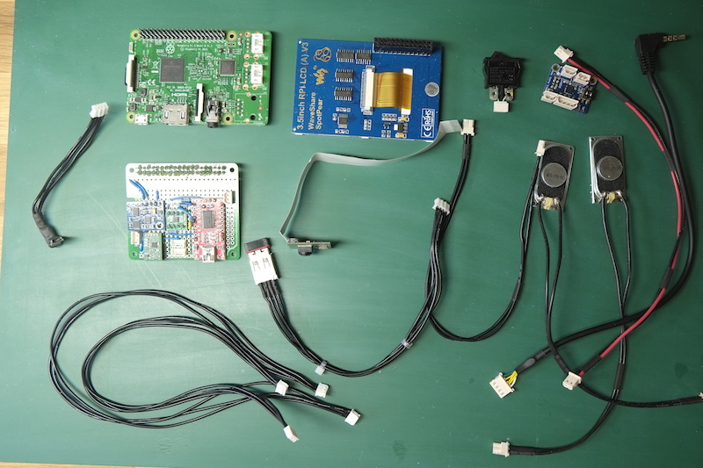
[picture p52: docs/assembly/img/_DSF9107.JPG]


* One "Diet" Raspberry Pi 3
* One 3.5inch LCD from Waveshare
* One interface board that includes the Dynamixel bus adapter, power regulator and a 9DOF IMU
* One 2x2W power amplifiers from Adafruit, model [1552](https://www.adafruit.com/products/1552)
* One Raspberry Pi camera
* Two 20x40 speakers with cables and connectors (you can choose a different way to connect the speakers to the aplifier board - but it makes it easier to assemble and dissassemble the head if they have connectors)
* A custom USB cable that can connect to the JST plugs on the on the Slim Raspberry Pi board and has a normal USB B socket on the other side
* One WiFi dongle (that you know for sure works with Raspberry Pi); we will use the built in WiFi to create an access point (thus allowing us to connect from another computer to the Poppy no matter where we are located and if there is a WiFi or not) and this second WiFi we will use to connect to an exiting WiFi network. We will activate NAT so that Poppy will act as a normal access point when connected to another WiFi.
* One power switch; the model I use is from Maplin [N19CL](http://www.maplin.co.uk/p/slim-line-rocker-switch-n19cl) but there are other producers with the same characteristics
* A set of other custom cables: 1 two wires for the power of the audio amplifier, 1 two wires for the connection of the switch, one audio jack (stereo 3.5mm) to 4 pin MOLEX for the audio amplifier and 1 Mini USB to JST for the connection of the FT232 serial board that is used for the Dynamixel bus. All these cables are dependent on what connectors you decide to use (if any) on the boards but I strongly recommend you to use connectors at least on one of the sides of the cable in case you want to solder the other side on the boards
* One 300mm Dynamixel XL cable (custom made)
* One 400mm Dynamixel XL cable (custom made)

First we will need to put in place the 3 heat serts in the front head in the 3 holes avaialable. Use a soldering iron set to about 170 degrees Celsius and make sure that the heat sert is positioned sqare with the face of the hole and do not apply pressure; let the the heat sert sunk into the plastic slowly until is flush with the hole face:

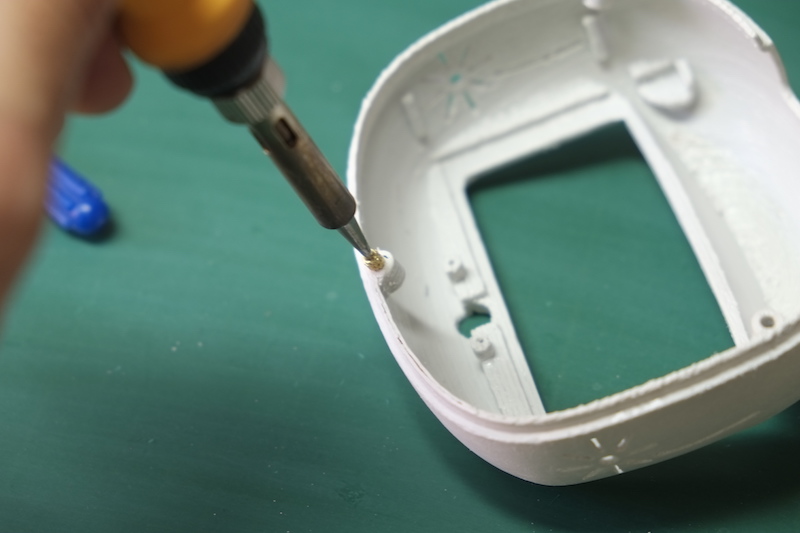
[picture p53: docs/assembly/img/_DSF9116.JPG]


Once you place all three heat serts into the head it would be a good idea to use the three screws and mount the front and the back of the head making sure that the screws work fine and that there was no misalignment of the axes:

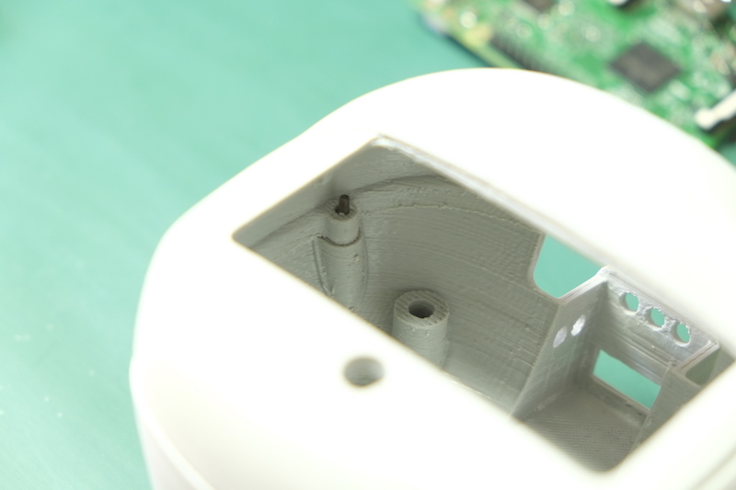
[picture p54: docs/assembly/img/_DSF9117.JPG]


Place now the 3.5inch Waveshare LCD screen into the head front with the pin header connector positioned towards the lower part of the head. The screen should fit just enough in the frame without needing too much preasure, but also without being loose:

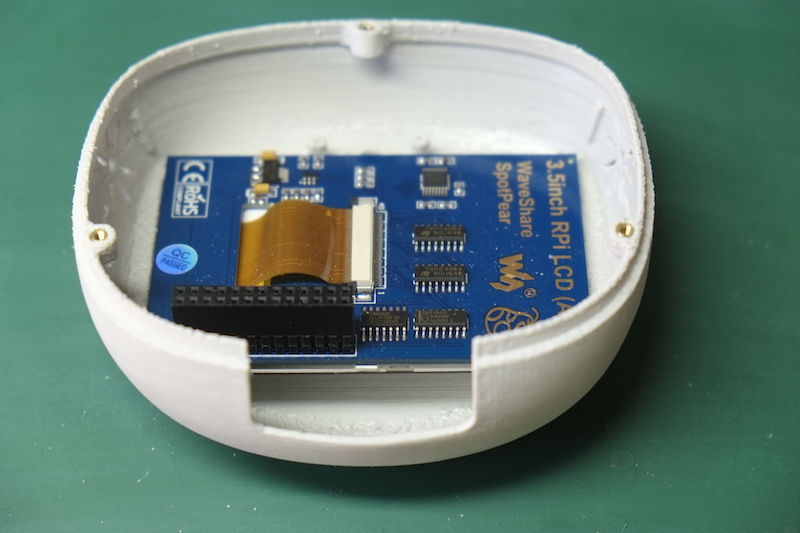
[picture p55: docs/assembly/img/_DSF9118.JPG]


Check on the front that there is no gaps left between the screen and the inside edges of the frame. If there is a gap this indicates that the screen did not sit properly in the frame and you should check if there are parts or leftovers from printing that are in the way.

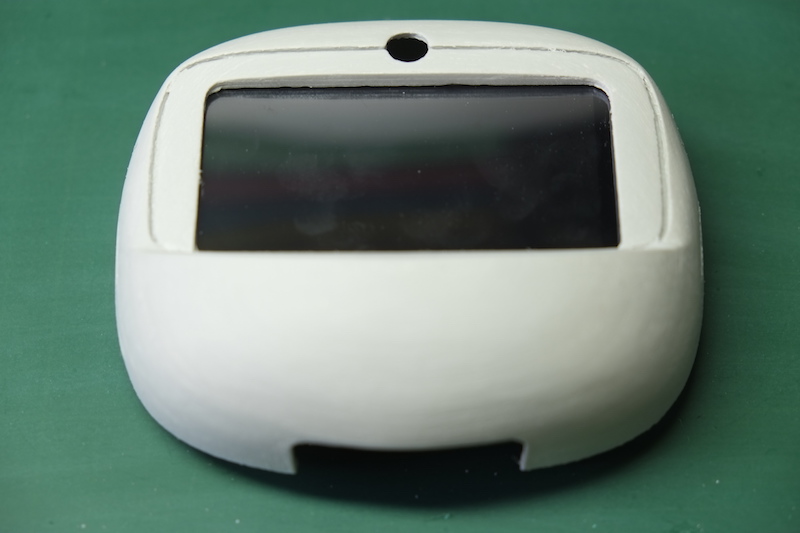
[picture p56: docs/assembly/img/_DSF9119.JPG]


Place a few centimeters of isolation band on the LCD board in the centre between the two pillars that will hold the camera. This is to make sure that the two board do not produce any shorts:

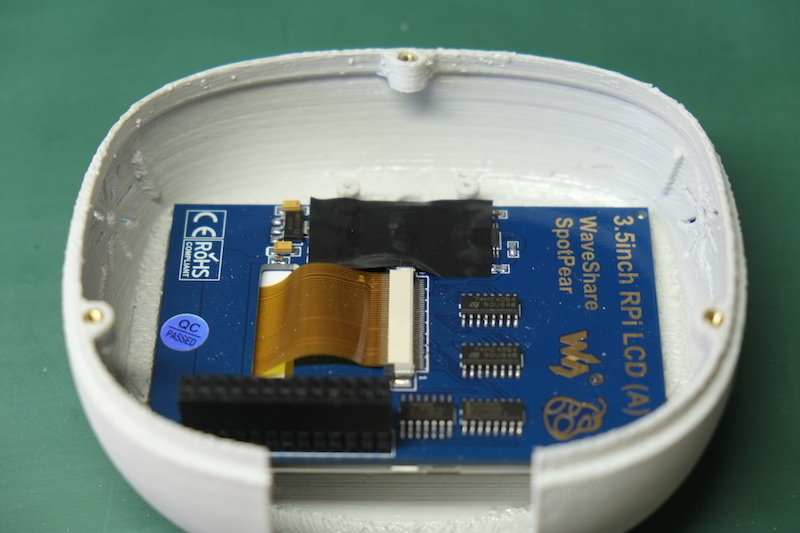
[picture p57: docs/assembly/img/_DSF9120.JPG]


Now place the Raspberry Pi camera over the LCD screen and the isolation band and secure it in position using two M2x4mm self tap screws:

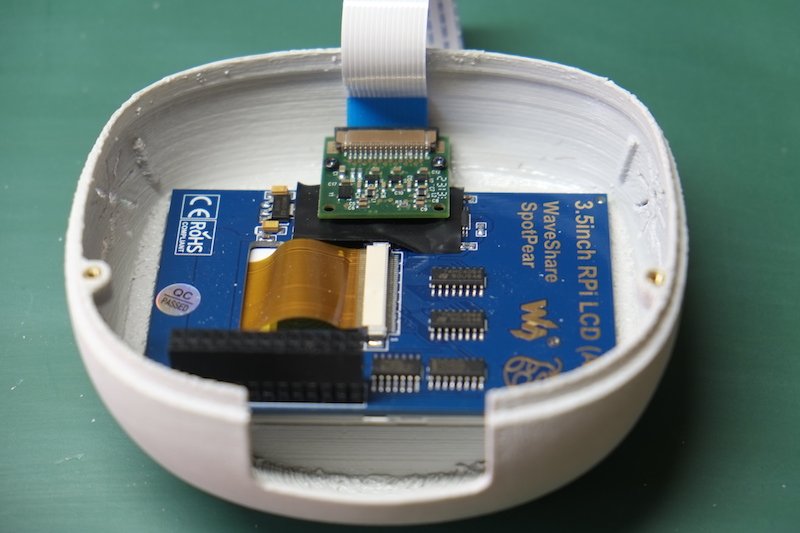
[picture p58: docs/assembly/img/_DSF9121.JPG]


Place the two speakers in the sides of the head. They should fit snugly between the two supports and you will have to use a little bit of pressure to have them sit in place.

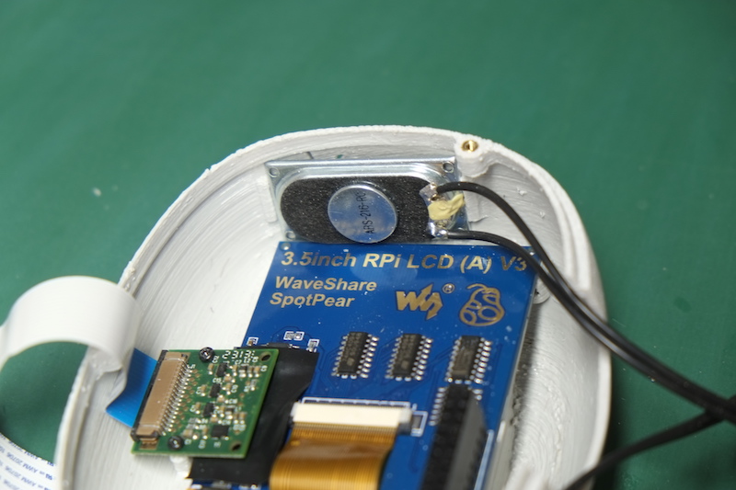
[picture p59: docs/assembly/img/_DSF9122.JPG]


Now we'll prepare the HAT board by connecting all the cables to it: the 2 custom Dynammixel cables (30 and 40cm) will go to the XL connectors, the power cable and the switch cable onto their dedicated connectors:



Connect two M-F 15mm standoffs and two F-F 12mm standoffs as in the picture bellow in the holes opposite the GPIO on the Raspberry Pi. The long standoffs are on the front of the board, the short ones on the back of the board:



Connect the remaining F-F 12mm standoffs in the holes next to the GPIO on the back of the board using 2 M2x6mm screws:



Place the HAT board onto the LCD screen making sure the pins are corectly alligned (the HAT has 2x20 and the screen has 2x13 - you need to make sure that the outside pins are properly aligned). The pin header on the LCD will limit the ditance on that side while the 15mm standoffs will limit the position of the HAT in respect to the screen:



Add the custom USB cable into the mini USB connector on the FT232 board:



Connect this cable to the USB connector in the middle on the front of the Raspberry Pi and also connect the flat ribbon from the camera to the camera connector:



Carefully place the Raspberry Pi on top of the HAT board making sure the GPIO connector is aligned properly and taking care of the camera ribbon:



Take the custom USB dongle cable and place the USB female connector in one of the supports in the head back. It should slide relatively easy as long as you make sure there are no leftovers from the 3D printing process in that support:



Place the WiFi dongle in the USB connector:



Mount the power amplifier using 2 M2x4mm self tap screws at the back of the head:



Slide the switch into its place at the back of the neck:



Use two 10mm round guards and stick them onto the spacers (they are self adhesive):



And place these spacers in the holes in the head back:



Take the XL-320 servo (id 37) and connect it to the neck 3D part as in the picture using 4 rivets. Add a standard XL cable on the undersidide:



And one 3-step rivet on the other side:



Now slide the servo into the neck back and secure it with 3 rivets on the underside:



As well as two more on each side:



Connect all the cables between the two parts of the head: speakers to the power amplifier, power to the amplifier, power switch and the audio cable from the audio jack of the Rasbperry Pi:



Guide the 2 long Dynamixel cables through the hole at the back of the neck behind the switch:



Gently close the head making sure that the cables do not misbehave and get into the way. In principle they should be nicely sitting through the middle of the head allowing you to align the holes with the screws and to secure eveything up:



Make sure the long Dynamixel cables are coming out as much as allowed and that they do not get tangled inside:



This is it! We now can start putting it all together in the next guide.

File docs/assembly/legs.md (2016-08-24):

# Legs assembly

I will show you here only the assembly steps for the **left leg**. The right leg follows the same steps except that some parts are in mirror. I will give you the appropriate hints bellow when there is someting you need to take care.

For the assembly of Poppy's left leg you will need:
_DSF9070

1. The left foot
2. The left shin
3. The left thigh
4. One hip connector
5. The left hip
6. 4 Dynamixel XL-320 servos already configured with the IDs: 12, 13, 14 and 15 (for right leg they will be 22, 23, 24 and 25)
7. 3 Dynamixel cables - the standard ones that came with the servos
8. One 160mm Dynamixel cable
9. One short Dynamixel cable - these are cables that were made from one standard XL-320 cable that was cut in two and connectors were added to the cut sides. Unlike the AX cables, Robotis does not sell cables shorter than 110mm for XL-320 and for some assemblies that is too long and can get in the way of other moving parts. We might try to see if it would be possible to produce some custom cables that can be commercialized in the future, but if you are really interested in robotics with Dynamixel servos it might be a good idea to invest in a relativelly unexpensive but reliable crimper and stripper. Alternativelly you can chose to use the standard 110mm cables instead of the shortered ones, but be careful obout how they are routed.
10. One [hot-swap board](../../hardware/electronics/hotswap.md); you can get the information about this board [here]
11. 44 2-step OLLO rivets
12. 3 3-step OLLO rivet
13. 4 M2x4mm self-tap screws (I'm using the ones from the Bioloid kit under the code S11 - but any self-tap screws that are 2mm in diameter should do it)

We will first secure in postion the hot-swap board on the shin using the 4 self-tap screws:

_DSF9073

The  hot-swap board has on the back side two jumper pins that should be perfectly aligned with the hole in the shin's back. You can test that by using a LiPo battery pushing the power connector of the battery through the hole and making sure that is connects true with the pins in the hot-swap board. It would also be good to verify at this moment that this hole has preserved it's shape and allows you to connect the battery plug only one way around, preventing you to insert it the wrong way around:

_DSF9074

Take the servo id 15 (25 for the right foot) and connect the short Dynamixel cable (or a normal one if you cannot make the shorter ones) as shown in the picture (for the right foot the servo will be facing the other way around - remember in the Poppy Seed the horns are always on the outside):

_DSF9075

Slide now the servo in the shin making sure that the horn is facing towards right (in the case of the right leg it will face left). Secure it in position using 3 rivets on the front side of the shin:

_DSF9076

Then add 3 more rivets on the horn side:

_DSF9077

And another 3 on the idle side:

_DSF9078

Connect the cable from the servo to the outermost connector from the hot-swap board:

_DSF9079

Take now the servo 14 (or 24 for the right foot) and connect the backside conctor with a standard cable. The position of the servo is with the horn down and towards exterior (right for the left foot - the other way aqround for the right foot):

_DSF9080

Place the servo in his position on the shin and secure it with 4 rivets to the horn:

_DSF9081

And one 3-step rivet on the idle side:

_DSF9082

Connect the cable from this servo to the free connector in the hot-swap board:

_DSF9098

Take the 160mm cable and connect it on the front connector of the knee servo as seen in the picture:

_DSF9083

Slide the thigh over the servo and secure with 3 rivets on one side:

_DSF9084

And 3 more rivets on the other side:

_DSF9085

Take the servo 12 (22 for the right foot) and connect the 2 remaining standard cables directing them towards the back of the servo:

_DSF9086

Carefully slide the servo in the hip making sure that the horn ends up in the hole and the cables are exiting the back of the hip. Make sure that the horn is set to 0 before doing this: it is quite difficult to see the markings on the horn once in position because there is relatively little clearance between the horn and the hip hole:

_DSF9087

Secure the servo in position with 2 rivets on the side:

_DSF9088

3 more rivets on the other side:

_DSF9089

And 3 more rivets on the underside:

_DSF9090

Place the hip connector part on the horn of the servo and secure it with 4 rivets as seen in the picture:

_DSF9091

Take the cable that is on the exterior of the hip and connect it to the upper connector of the servo 13 (23 for the right leg). The servo 13 will be positioned with (you guessed it...) the horn outside:

_DSF9092

Slide the servo 13 into the hip connector and then secure it with 3 rivets on the underside:

_DSF9093

Rotate the hip conector 90 degrees so that the holes on the upper part become accessible and add two more rivets on the upper part (the one in the middle stays empty because the cable):

_DSF9094

Rotate the hip connector back in the normal position and connect now the horn of the servo 13 with the thigh securing it with 4 rivets:

_DSF9095

And a 3-step rivet on the idle side:

_DSF9096

Rotate the thigh so that the underside connector of the servo 13 is accessible and connect the long cable coming from the knee to this servo:

_DSF9097

Now connect the left foot to the servo 15 using 4 rivets on the horn side:

_DSF9099

And a 3-step connector on the idle side:

_DSF9100

Congratulations, you have finished the assembly of the left foot. The pelvis will be connected later in the final assembly.

_DSF9101

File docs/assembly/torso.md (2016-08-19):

# Torso Assembly

To assembly the Poppy Seed torso you will need the following:



* The 3D printed Chest
* The 3D printed Spine
* The 3D printed Abdomen
* One XL-320 combo (dual) for the upper torso with the servo IDs 34 and 35. Please follow [this guide](dualXL.md) for details about how to put this together.
* One XL-320 combo (dual) for the lower torso with the servo IDs 31 and 32. Use the same guide but please make sure you use the indicated 160mm cable in the assembly
* 4 Dynamixel XL-320 with the IDs: 33 (spine), 36 (neck Z), 41 (left shoulder) and 51 (right shoulder)
* 2 110mm Dynamixel cables (the ones that come standard with the servo)
* 3 160mm Dynamixel calble
* 38 2-step OLLO rivets
* 3 3-step OLLO rivets

Start by adding one long (160mm) and one normal cable to the servo 41 (left shoulder):



Since this is the left shoulder it will be mounted on the right as we look forward at the chest. The horn will face towards outside - so right - and the long cable will be connected to the underside of the servo while the normal cable to the upper side as you can see in the picture.

Now slide the servo in position in the chest one the right side as we look at the chest from front. The upper cable should be directed between the servo's supports:



Secure the servo in position with three rivets on the outside:



And add four more rivets on the inside of the chest:



Guide the longer (underside) cable through the hole in the chest and pull it out through the cetral hole:



Repeat the process with the right shoulder servo (51) making sure that they are in mirror. The underside should use the longer cable and the upperside the normal cable. Slide the servo in position:



Then secure it with 3 rivets on the outside and 4 on the inside in the same way we have done for the left shoulder. Guide the underside cable through the hole in the chest and pull it through the cetre hole:



Place the servo 36 (neck) on top of the chest:



And secure it from bellow with 6 rivets as shown in the following picture:



Take the upper XL combo and guide the longer cable through the centre hole in the chest towards the servo 36:



Pull that cable out on the top of the chest next to the servo 36:



And connect it to one side of the servo 36:



Now secure the combo on the chest using 4 2-step rivets to secure the horn:



And one 3-step rivet on the other side:



Connect now the two cables coming from the shoulders (through the channels and the central hole in the chest) to the two back most connectors in the hub:



Put the assembled chest to the side and take the abdomen and the servo with ID 33. Place it on top of the abdomen as in the following picture:



Secure it in position with 4 rivets:



Take the lower XL combo and slide the longer cable through the hole in the abdomen:



Use four rivets to secure the lower combo horn with the abdomen:



And one 3-step rivet on the other side:



Connect the cable to the servo on the spine (ID 33) - it doesn't matter on which side you will connect it:



Now slide the spine in position from the front of the servo towards the back until the holes are aligned.



Secure the servo in position using six rivets:



You can now combine the lower part of the torso with the upper part. Place the upper part Y axis servo in position between the spine's holders and fix it with four rivets one the horn side:



And one 3-step rivet on the the other side:



Take the last remaining 160mm cable and cut the Data wire. Look carefully at the position of the connector and cut the same cable on the outside (the picture is of a cable made by myself - but it is easier if you use a standard 160mm cable and cut the Data cable). The reason we are cutting the Data cable is that we want to isolate the upper part of the body from the lower part in the case we are able to use a controller that has 2 channels. But we need to cable to improve the power transmission from the legs (that have the batteries) to the upper body.



Connect this cable to the middle coonnector in both hubs and guide it through the abdomen hole:



Your Poppy Seed abdomen is now ready!



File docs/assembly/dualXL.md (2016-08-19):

# Dual XL-320 Assembly

You will need two assemblies of XL-320 in the torso: one in the upper part and one in the lower part. They provide the X-Y DOF for that part of the body. Unfortunatelly there are no standard parts from Robotis that allows the XL-320 to be mounted in a 90 degree position, so we will have to print some parts that will fulfill this scope.

The assembly instructions will apply to both the upper and lower torso, the only difference will be the IDs of the servos you will use.

To build a dual XL-320 assembly you will need:



* 2 Dynamixel XL-320 preconfigured with the IDs (34, 35 for the upper torso and 31, 32 for the lower torso)
* 2 Dual XL mount 3D printed parts
* 1 Dual XL idle 3D printed part (in the picture there is an older version of the part, the one in the STL repository is slighly different, but not that much)
* 2 short XL cables: these are cables that were made from one standard 110mm XL-320 cable that was cut in two and connectors were added to the cut sides. Unlike the AX cables, Robotis does not sell cables shorter than 110mm for XL-320 and for some assemblies that is too long and can get in the way of other moving parts. We might try to see if it would be possible to produce some custom cables that can be commercialized in the future, but if you are really interested in robotics with Dynamixel servos it might be a good idea to invest in a relativelly unexpensive but reliable crimper and stripper. Alternativelly you can chose to use the standard 110mm cables instead of the shortered ones, but be careful obout how they are routed.
* 1 normal XL cable 110mm (for the lower combo you will need a 160mm cable from Dynamixel)
* 1 custom made XL hub; this is the equivalent of the AX hub produced by Robotis that allows you to connect 3 cables together. Unfortunatelly there is no equvalent for XL servos, so we'll have to make it ourselved. The one you see is made on a simple strip board simply soldering 5 XL Molex connectors and adding 2 4mm holes that we will use to rivet the board in place.
* 18 2-step OLLO rivets
* 2 3-step OLLO rivets

Before we start building the assembly let's first understand what we will build and define some rules. The dual mount will position one of the servos on the Y axis and one on the X axis. Specifically the front servo will provide the Y DOF and the back servo the X DOF. The front servo will be positioned with the horn to the right (as seen from front) in order to mate properly with the next part in the assembly while the back servo will be positioned with the horn on the back. Both servos will have the horns on the the lower side (i.e. the bodies are upwards). The front servo will have the lower number and the back servo the higher number. This picture will give you some idea and it would be a good excersise to place the servos in this position before starting the assembly:



Now let's start the build! Take the front servo (34 for upper torso and 31 for lower torso) and connect one short cable on the connector that is at the back of the servo (inside, between the two servos). This will be the cable that will connect the two servos:



Now add the two dual mounts using three rivets each making sure that the cable is flowing nicely between them:



Connect the short cable to the second servo (35 for the upper torso and 32 for the lower torso) as seen in the picture bellow. Connect the longer cable to the other port of the second servo:



Now put the second servo in position between the XL dual mounts making sure that the cables are nicely flowing between them. Fix the servo on one side using four rivets:



Add 4 more rivets on the other side:



Add now the second short cable to the free connector at the front of the first servo and bend it 180 degrees so that it exits to the left as seen from front:



Place the XL idle on top of the front of the first servo, making sure that the cable is guided between the two mount holes of the servo. Fix the XL idle using four rivets as shown in the picture. The two rivets on the idle circle should be flush with the surface and if you place your finger over that sourface you should not feel them sticking out.



Guide the long XL cable towards the center of the assembly and then place the XL hub over the dual XL mount, aligning the holes. The 45 degrees cuts in the hub should face down. Fix the hub in place using two 3-step rivets:



Connect the short cable coming from the front servo to the first connector in the hub:



This concludes the build of the dual XL mount. Two of the connectors in the hub will be used by the limbs that are linked to the chain (arms for the upper torso and legs for the lower torso), one of the connector will be used to add some power redudancy between the two hubs and the remaining connector in each hub will be connected with a cable to the controller in the head.

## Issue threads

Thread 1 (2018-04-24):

onshape Shared development authority

nan2854, 2018-04-24:
I want onshape development share permissions can be my name Chen Shina  陈仕南   onshape 106425
3905 @qq.com

sonelu, 2018-05-08:
@nan2854 You can clone the project under your workspace in OnShape and perform any modifications you want.

Closed 2018-05-08.

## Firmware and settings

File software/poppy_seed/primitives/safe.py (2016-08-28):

from __future__ import division
import platform
import logging
import subprocess

import pypot.primitive

logger = logging.getLogger(__name__)

class LimitTorque(pypot.primitive.LoopPrimitive):
    def __init__(self, robot, freq=20, max_error=10., torque_min=20., torque_max=95.):
        pypot.primitive.LoopPrimitive.__init__(self, robot, freq)

        self._max_error = max_error
        self.torque_min = torque_min
        self.torque_max = torque_max

    def setup(self):
        self.initial_torque_limit = []

        # Using a dictionnary may be a better solution so we can easily retrieve the initial torque value.
        for m in self.robot.motors:
            self.initial_torque_limit.append(m.torque_limit)

        self.active_motors = self.robot.motors

    def update(self):
        for m in self.active_motors:
            self.adjust_torque(m)

    def adjust_torque(self, motor):
        target = motor.goal_position
        pos = motor.present_position
        dist = abs(target - pos)

        if dist > self._max_error:
            motor.torque_limit = self.torque_max
        else:
            motor.torque_limit = self.torque_min + dist / self._max_error * (self.torque_max - self.torque_min)

    def teardown(self):
        for m, i in enumerate(self.robot.motors):
            m.torque_limit = self.initial_torque_limit[i]

    @property
    def change_watched_motors(self):
        return self.active_motors

    @change_watched_motors.setter
    def change_watched_motors(self, watched_motors):
        self.active_motors = map(self.get_mockup_motor, watched_motors)

    @property
    def max_error(self):
        return self._max_error

    @max_error.setter
    def max_error(self, new_error):
        if new_error <= 0:
            raise ValueError('The max_error parameter must be strictly positive!')
        self._max_error = float(new_error)

    # TODO
    @property
    def add_watched_motors(self):
        raise NotImplementedError('TODO :)')

    @add_watched_motors.setter
    def add_watched_motors(self, added_motors):
        raise NotImplementedError('TODO :)')

    @property
    def remove_watched_motors(self):
        raise NotImplementedError('TODO :)')

    @remove_watched_motors.setter
    def remove_watched_motors(self, suppressed_motors):
        raise NotImplementedError('TODO :)')


class TemperatureMonitor(pypot.primitive.LoopPrimitive):
    '''
        This primitive raises an alert by playing a sound when the temperature
        of one motor reaches the "temp_limit".
        
        On GNU/Linux you can use "aplay" for player
        On MacOS "Darwin" you can use "afplay" for player
        On windows vista+, you can maybe use "start wmplayer"
        '''
    def __init__(self, robot, freq=0.5, temp_limit=55, player=None, sound=None):
        pypot.primitive.LoopPrimitive.__init__(self, robot, freq)

        self.temp_limit = temp_limit
        self.sound = sound
        self.watched_motors = self.robot.legs + self.robot.torso + self.robot.arms
        
        if player is not None:
            self.player = player
        elif 'Windows' in platform.system():
            self.player = 'wmplayer'
        elif 'Darwin' in platform.system():
            self.player = 'afplay'
        else:
            self.player = 'aplay'

    def setup(self):
        pass

    def update(self):
        self.check_temperature()

    def teardown(self):
        pass

    def check_temperature(self):
        motor_list = []

        for m in self.watched_motors:
            if m.present_temperature > self.temp_limit:
                motor_list.append(m)

        if len(motor_list) > 0:
            self.raise_problem(motor_list)

    def raise_problem(self, motor_list):
        try:
            subprocess.call([self.player, self.sound])
        except OSError:
            logger.warning('Sound player {} cannot be started'.format(self.player))

        for m in motor_list:
            print('{} overheating: {}'.format(m.name, m.present_temperature))

class VoltageMonitor(pypot.primitive.LoopPrimitive):
    '''
        This primitive raises an alert by playing a sound when the voltage
        on the bus goes bellow "volt_limit".
        
        On GNU/Linux you can use "aplay" for player
        On MacOS "Darwin" you can use "afplay" for player
        On windows vista+, you can maybe use "start wmplayer"
        '''
    def __init__(self, robot, freq=0.1, volt_limit=7.0, player=None, sound=None):
        pypot.primitive.LoopPrimitive.__init__(self, robot, freq)

        self.volt_limit = volt_limit
        self.sound = sound
        self.watched_motors = self.robot.legs + self.robot.torso + self.robot.arms
        
        if player is not None:
            self.player = player
        elif 'Windows' in platform.system():
            self.player = 'wmplayer'
        elif 'Darwin' in platform.system():
            self.player = 'afplay'
        else:
            self.player = 'aplay'

    def setup(self):
        pass

    def update(self):
        self.check_voltage()

    def teardown(self):
        pass

    def check_voltage(self):
        min_voltage = 20

        for m in self.watched_motors:
            if m.present_voltage < min_voltage:
                min_voltage = m.present_voltage
        logger.info('Voltage: {} V'.format(min_voltage))

        if min_voltage < self.volt_limit:
            self.raise_problem(min_voltage)

    def raise_problem(self, min_voltage):
        try:
            subprocess.call([self.player, self.sound])
        except OSError:
            logger.warning('Sound player {} cannot be started'.format(self.player))

        print('Low voltage: {} V'.format(min_voltage))

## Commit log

2016-08-07 Added new STLs
    [arm connector small.stl]
2016-08-07 Arms assembly
2016-08-15 Added head and some of torso
    [dual XL idle.stl, dual XL mount.stl, neck small.stl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]
2016-08-19 Pictures for torso assembly
2016-08-22 Legs STLs and pictures
    [hip connector.stl]
2016-08-22 Pictures for legs assembly
2016-08-24 Legs assembly
2016-08-27 Last assembly pics
